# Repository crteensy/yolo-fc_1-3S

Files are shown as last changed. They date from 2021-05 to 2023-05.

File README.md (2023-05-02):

# Yolo FC, STM32F7, 1-3S
This FC has been test flown with a 3" toothpick, and it flew well.

- Main MCU: STM32F745
- IMU: ICM-20602
- Flash: 8MB
- Baro: BMP280
- OSD: '7456
- GNSS: Integrated GPS module (uBlox ZOE-M8Q) with u.Fl connector and experimental support for active antennas
- 4 ESCs:
  - EFM8BB21 / bluejay
  - Calculated current rating of 20A continuous 30A burst (depending on the airflow cooling situation)
- Current sensor: INA186 with 0m5 shunt - subjectively some of the best current measurements we have seen on any FC
- 4 multi purpose expansion connectors:
  - each with its own UART
  - shared I2C bus
  - 5V, 3V3 and GND
  - a multi-purpose pin for analog RSSI, Buzzer, LEDs, etc.
- One video expansion connector:
  - Camera in and VTx out
  - UART
  - 2 multi-purpose pins
  - switchable 5V (*)
- size: 30 x 25.2 mm

The expansion connectors can be used with very simple or more complex plug-ins for
- Rx of your choice
- Magnetometer
- Buzzer
- LED strip
- dual camera switching on the OSD connector
- even additional plugin ESCs for hexa- and octocopters are possible

*) The OSD connector has a 5V output that is only ON when USB is not plugged in. This protects your USB port from power hungry VTx'es that might overload the port. However, that feature can be disabled with a solder bridge.

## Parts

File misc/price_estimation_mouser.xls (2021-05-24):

C6 | 10µF | AMK107ABJ106KAHT | 0.053 | 0.149 | 0.041 | 1
C7 | 100nF | GMK105BJ104KV-F | 0.019 | 0.077 | 0.014 | 1
C8 | 10µF | AMK107ABJ106KAHT | 0.053 | 0.149 | 0.041 | 1
C9 | 100nF | GMK105BJ104KV-F | 0.019 | 0.077 | 0.014 | 1
C10 | 100nF | GMK105BJ104KV-F | 0.019 | 0.077 | 0.014 | 1
C11 | 10µF | AMK107ABJ106KAHT | 0.053 | 0.149 | 0.041 | 1
C12 | 220µF | 6TPE220MAZB | 0.817 | 1.08 | 0.544 | 1
C13 | 220µF | 6TPE220MAZB | 0.817 | 1.08 | 0.544 | 1
C14 | 1µF | LLA215C70G105MA14K | 0.149 | 0.248 | 0.066 | 1
C15 | 2.2µF | LLA219C70G225MA01L | 0.127 | 0.213 | 0.066 | 1
C16 | 100nF | GMK105BJ104KV-F | 0.019 | 0.077 | 0.014 | 1
C17 | 100nF | GMK105BJ104KV-F | 0.019 | 0.077 | 0.014 | 1
C18 | 100nF | GMK105BJ104KV-F | 0.019 | 0.077 | 0.014 | 1
C19 | 100nF | GMK105BJ104KV-F | 0.019 | 0.077 | 0.014 | 1
C20 | 1µF | LLA215C70G105MA14K | 0.149 | 0.248 | 0.066 | 1
C21 | 2.2µF | LLA219C70G225MA01L | 0.127 | 0.213 | 0.066 | 1
C22 | 2.2µF | GRM188R6YA475KE15D | 0.11 | 0.113 | 0.104 | 1
C23 | 2.2µF | GRM188R6YA475KE15D | 0.11 | 0.113 | 0.104 | 1
C24 | 2.2µF | GRM188R6YA475KE15D | 0.11 | 0.113 | 0.104 | 1
C25 | 2.2µF | GRM188R6YA475KE15D | 0.11 | 0.113 | 0.104 | 1
C26 | 10µF | TCJA106M025R0150 | 0.351 | 0.512 | 0.212 | 1
C27 | 10µF | TCJA106M025R0150 | 0.351 | 0.512 | 0.212 | 1
C28 | 100nF | C0603X5R1E104K030BB | 0.037 | 0.03 | 0.022 | 1
C29 | 100nF | GMK105BJ104KV-F | 0.019 | 0.077 | 0.014 | 1
C30 | 100nF | GMK105BJ104KV-F | 0.019 | 0.077 | 0.014 | 1
C31 | 100nF | GMK105BJ104KV-F | 0.019 | 0.077 | 0.014 | 1
C32 | 100nF | GMK105BJ104KV-F | 0.019 | 0.077 | 0.014 | 1
C33 | 100nF | C0603X5R1E104K030BB | 0.037 | 0.03 | 0.022 | 1
C34 | 100nF | GMK105BJ104KV-F | 0.019 | 0.077 | 0.014 | 1
C35 | 10µF |  | 0.077 | 0.114 | 0.69 | 1
C36 | 10µF |  | 0.077 | 0.114 | 0.69 | 1
C37 | 1µF | EMK105BJ105MVHF | 0.025 | 0.038 | 0.022 | 1
C38 | 100nF | C0603X5R1E104K030BB | 0.037 | 0.03 | 0.022 | 1
C39 | 10µF | AMK107ABJ106KAHT | 0.053 | 0.149 | 0.041 | 1
C40 | 100µF | T55A107M6R3C0045 | 0.418 | 0.739 | 0.369 | 1
C41 | 1µF | LLA215C70G105MA14K | 0.149 | 0.248 | 0.066 | 1
C42 | 2.2µF | LLA219C70G225MA01L | 0.127 | 0.213 | 0.066 | 1
C43 | 1µF | LLA215C70G105MA14K | 0.149 | 0.248 | 0.066 | 1
C44 | 2.2µF | LLA219C70G225MA01L | 0.127 | 0.213 | 0.066 | 1
C45 | 2.2µF | GRM188R6YA475KE15D | 0.11 | 0.113 | 0.104 | 1
C46 | 2.2µF | GRM188R6YA475KE15D | 0.11 | 0.113 | 0.104 | 1
C47 | 100nF | C0603X5R1E104K030BB | 0.037 | 0.03 | 0.022 | 1
C48 | 47µF | TCSOM0J476M8R-ZM1 | 0.718 | 0.432 | 0.381 | 1
C49 | 22µF | TCSOM0J476M8R-ZM1 | 0.781 | 0.432 | 0.381 | 1
C50 | 2.2µF | C0402C225M9PACTU | 0.093 | 0.08 | 0.043 | 1
C51 | 2.2µF | C0402C225M9PACTU | 0.093 | 0.08 | 0.043 | 1
C52 | 2.2µF | C0402C225M9PACTU | 0.093 | 0.08 | 0.043 | 1
C54 | 100nF | C0603X5R1E104K030BB | 0.037 | 0.03 | 0.022 | 1
C55 | 2.2µF | GRM188R6YA475KE15D | 0.11 | 0.113 | 0.104 | 1
C56 | 2.2µF | GRM188R6YA475KE15D | 0.11 | 0.113 | 0.104 | 1
D1 | True Green | SML-LX0201UPGC-TR | 0.224 | 0.091 | 0.075 | 1
D2 | SBR1A30T5-7 | SBR1A30T5-7 | 0.197 | 0.317 | 0.125 | 1
D3 | Blue | SML-LX0201USBC-TR | 0.218 | 0.088 | 0.073 | 1
D4 | White | SML-LX0201NWD-TR | 0.273 | 0.121 | 0.096 | 1
FB3 | 120R@100Mhz | BLM18SG121TN1D | 0.064 | 0.043 | 0.039 | 1
FB4 | 120R@100Mhz | BLM18SG121TN1D | 0.064 | 0.043 | 0.039 | 1
FB5 | 120R@100Mhz | BLM18SG121TN1D | 0.064 | 0.043 | 0.039 | 1
FB6 | 120R@100Mhz | BLM18SG121TN1D | 0.064 | 0.043 | 0.039 | 1
J1 | USB_B_Micro |  | 0.667 | 0.618 | 0.488 | 1
J2 | 10132797-011100LF |  | 0.36 | 0.315 | 0.247 | 1
J3 | 10132797-011100LF |  | 0.36 | 0.315 | 0.247 | 1
J4 | 10132797-011100LF |  | 0.36 | 0.315 | 0.247 | 1
J5 | 10132797-011100LF |  | 0.36 | 0.315 | 0.247 | 1
J6 | 10132797-011100LF |  | 0.36 | 0.315 | 0.247 | 1
L2 | 470nH | MCKK1608TR47MN | 0.281 | 0.211 | 0.145 | 1
L3 | 1µH | SRP2512A-1R0M | 0.333 | 0.237 | 0.171 | 1
L4 | 39nH | MLG0603P39NHT000 | 0.032 | 0.029 | 0.021 | 1
Q1 | DMP2066LSN-7 |  |  |  |  | 1
R1 | 100k |  | 0.05 | 0.02 | 0.01 | 1
R2 | 24k9 |  | 0.05 | 0.02 | 0.01 | 1
R3 | 75R |  | 0.05 | 0.02 | 0.01 | 1
R4 | 10k |  | 0.05 | 0.02 | 0.01 | 1
R5 | 470R |  | 0.05 | 0.02 | 0.01 | 1
R6 | 75R |  | 0.05 | 0.02 | 0.01 | 1
R7 | 470R |  | 0.05 | 0.02 | 0.01 | 1
R8 | 1k |  | 0.05 | 0.02 | 0.01 | 1
R9 | 100R |  | 0.05 | 0.02 | 0.01 | 1
R10 | 470R |  | 0.05 | 0.02 | 0.01 | 1
R11 | 10R |  | 0.05 | 0.02 | 0.01 | 1
R12 | 2k2 |  | 0.05 | 0.02 | 0.01 | 1
R13 | 2k2 |  | 0.05 | 0.02 | 0.01 | 1
R14 | 2k2 |  | 0.05 | 0.02 | 0.01 | 1
R15 | 2k2 |  | 0.05 | 0.02 | 0.01 | 1
R16 | 2k2 |  | 0.05 | 0.02 | 0.01 | 1
R17 | 2k2 |  | 0.05 | 0.02 | 0.01 | 1
R18 | 2k2 |  | 0.05 | 0.02 | 0.01 | 1
R19 | 2k2 |  | 0.05 | 0.02 | 0.01 | 1
R20 | 2k2 |  | 0.05 | 0.02 | 0.01 | 1
R21 | 453k |  | 0.05 | 0.02 | 0.01 | 1
R22 | 100k |  | 0.05 | 0.02 | 0.01 | 1
R23 | 2k2 |  | 0.05 | 0.02 | 0.01 | 1
R24 | 2k2 |  | 0.05 | 0.02 | 0.01 | 1
R25 | 2k2 |  | 0.05 | 0.02 | 0.01 | 1
R26 | 2k2 |  | 0.05 | 0.02 | 0.01 | 1
R27 | 2k2 |  | 0.05 | 0.02 | 0.01 | 1
R28 | 2k2 |  | 0.05 | 0.02 | 0.01 | 1
R29 | 2k2 |  | 0.05 | 0.02 | 0.01 | 1
R30 | 2k2 |  | 0.05 | 0.02 | 0.01 | 1
R31 | 1k |  | 0.05 | 0.02 | 0.01 | 1
R32 | 1k |  | 0.05 | 0.02 | 0.01 | 1
R33 | 1k |  | 0.05 | 0.02 | 0.01 | 1
R34 | 1k |  | 0.05 | 0.02 | 0.01 | 1
R36 | 2k2 |  | 0.05 | 0.02 | 0.01 | 1
R37 | 2k2 |  | 0.05 | 0.02 | 0.01 | 1
R47 | 10k |  | 0.05 | 0.02 | 0.01 | 1
R48 | 1k |  | 0.05 | 0.02 | 0.01 | 1
R49 | 500µR | CST0612-FC-R0005-E | 0.466 | 0.336 | 0.279 | 1
R58 | 1k |  | 0.05 | 0.02 | 0.01 | 1
RN1 | 15k | TC124-FR-0715KL | 0.167 | 0.056 | 0.028 | 1
RN2 | 15k | TC124-FR-0715KL | 0.167 | 0.056 | 0.028 | 1
RN5 | 2k2 | YC104-FR-072K2L | 0.161 | 0.053 | 0.027 | 1
RN6 | 2k2 | YC104-FR-072K2L | 0.161 | 0.053 | 0.027 | 1
RN7 | 15k | TC124-FR-0715KL | 0.167 | 0.056 | 0.028 | 1
RN9 | 2k2 | YC104-FR-072K2L | 0.161 | 0.053 | 0.027 | 1
RN13 | 2k2 | YC104-FR-072K2L | 0.161 | 0.053 | 0.027 | 1
RN14 | 2k2 | YC104-FR-072K2L | 0.161 | 0.053 | 0.027 | 1
RN15 | 2k2 | YC104-FR-072K2L | 0.161 | 0.053 | 0.027 | 1
RN16 | 15k | TC124-FR-0715KL | 0.167 | 0.056 | 0.028 | 1
RN18 | 2k2 | YC104-FR-072K2L | 0.161 | 0.053 | 0.027 | 1
RN20 | 2k2 | YC104-FR-072K2L | 0.161 | 0.053 | 0.027 | 1
TP1 | PAD_B_ESC1 |  |  |  |  | 1
TP2 | PAD_A_ESC1 |  |  |  |  | 1
TP3 | PAD_B_ESC1 |  |  |  |  | 1
TP4 | PAD_C_ESC1 |  |  |  |  | 1
TP5 | PAD_B_ESC1 |  |  |  |  | 1
TP6 | PAD_C_ESC1 |  |  |  |  | 1
TP7 | PAD_C_ESC1 |  |  |  |  | 1
TP8 | PAD_A_ESC1 |  |  |  |  | 1
TP9 | BattPad+ |  |  |  |  | 1
TP10 | BattPad- |  |  |  |  | 1
TP11 | PAD_A_ESC1 |  |  |  |  | 1
TP12 | PAD_B_ESC1 |  |  |  |  | 1
TP13 | PAD_C_ESC1 |  |  |  |  | 1
TP14 | PAD_A_ESC1 |  |  |  |  | 1
TP15 | Prog |  |  |  |  | 1
TP16 | Prog |  |  |  |  | 1
TP17 | Prog |  |  |  |  | 1
TP18 | Prog |  |  |  |  | 1
TP19 | Prog |  |  |  |  | 1
TP20 | Prog |  |  |  |  | 1
TP21 | Prog |  |  |  |  | 1
TP22 | Prog |  |  |  |  | 1
TP23 | bridge |  |  |  |  | 1
TP29 | bridge |  |  |  |  | 1
TP30 | pad |  |  |  |  | 1
U1 | EFM8BB21F16G-C-QFN20R | EFM8BB21F16G-C-QFN20R | 0.59 | 0.556 | 0.556 | 1
U2 | EFM8BB21F16G-C-QFN20R | EFM8BB21F16G-C-QFN20R | 0.59 | 0.556 | 0.556 | 1
U3 | NCP81253MNTBG | NCP81253MNTBG | 0.64 | 0.413 | 0.272 | 1
U4 | SiZ200DT | SIZ200DT-T1-GE3 | 0.526 | 0.365 | 0.328 | 1
U6 | EFM8BB21F16G-C-QFN20R | EFM8BB21F16G-C-QFN20R | 0.59 | 0.556 | 0.556 | 1
U7 | NCP81253MNTBG | NCP81253MNTBG | 0.64 | 0.413 | 0.272 | 1
U8 | SiZ200DT | SIZ200DT-T1-GE3 | 0.526 | 0.365 | 0.328 | 1
U9 | NCP81253MNTBG | NCP81253MNTBG | 0.64 | 0.413 | 0.272 | 1
U10 | NCP81253MNTBG | NCP81253MNTBG | 0.64 | 0.413 | 0.272 | 1
U11 | SiZ200DT | SIZ200DT-T1-GE3 | 0.526 | 0.365 | 0.328 | 1
U12 | NCP81253MNTBG | NCP81253MNTBG | 0.64 | 0.413 | 0.272 | 1
U13 | SiZ200DT | SIZ200DT-T1-GE3 | 0.526 | 0.365 | 0.328 | 1
U14 | TPS62821 |  | 1.01 | 0.734 | 0.478 | 1
U15 | SiZ200DT | SIZ200DT-T1-GE3 | 0.526 | 0.365 | 0.328 | 1
U16 | NCP81253MNTBG | NCP81253MNTBG | 0.64 | 0.413 | 0.272 | 1
U17 | NCP81253MNTBG | NCP81253MNTBG | 0.64 | 0.413 | 0.272 | 1
U18 | NCP81253MNTBG | NCP81253MNTBG | 0.64 | 0.413 | 0.272 | 1
U19 | NCP81253MNTBG | NCP81253MNTBG | 0.64 | 0.413 | 0.272 | 1
U20 | SiZ200DT | SIZ200DT-T1-GE3 | 0.526 | 0.365 | 0.328 | 1
U21 | SiZ200DT | SIZ200DT-T1-GE3 | 0.526 | 0.365 | 0.328 | 1
U22 | SiZ200DT | SIZ200DT-T1-GE3 | 0.526 | 0.365 | 0.328 | 1
U23 | SiZ200DT | SIZ200DT-T1-GE3 | 0.526 | 0.365 | 0.328 | 1
U24 | EFM8BB21F16G-C-QFN20R | EFM8BB21F16G-C-QFN20R | 0.59 | 0.556 | 0.556 | 1
U25 | NCP81253MNTBG | NCP81253MNTBG | 0.64 | 0.413 | 0.272 | 1
U26 | SiZ200DT | SIZ200DT-T1-GE3 | 0.526 | 0.365 | 0.328 | 1
U27 | NCP81253MNTBG | NCP81253MNTBG | 0.64 | 0.413 | 0.272 | 1
U28 | NCP81253MNTBG | NCP81253MNTBG | 0.64 | 0.413 | 0.272 | 1
U29 | SiZ200DT | SIZ200DT-T1-GE3 | 0.526 | 0.365 | 0.328 | 1
U30 | SiZ200DT | SIZ200DT-T1-GE3 | 0.526 | 0.365 | 0.328 | 1
U31 | INA186 | INA186A2IDCKR | 1.12 | 0.811 | 0.529 | 1
U32 | LMR33630CQRNX |  | 8.88 | 7.5 | 7.13 | 1
U33 | STM32F745VGHx |  | 8.88 | 7.5 | 7.13 | 1
U34 | AB7456 |  | 2.387 | 2.255 | 2.18 | 1
U35 | ZOE-M8Q_ZOE-M8Q |  | 29 | 14.7 | 14.7 | 1
U36 | ICM-20602 |  | 2.26 | 1.59 | 1.25 | 1
U37 | S25FL064L |  | 2.25 | 1.97 | 1.75 | 1
U39 | BMP280 |  | 2.3 | 1.61 | 1.26 | 1
X1 | Molex_734120110 |  | 0.445 | 0.39 | 0.306 | 1
Y1 | CSTNE8M00G550000R0 |  | 0.184 | 0.147 | 0.131 | 1
Y2 | ECS-270-8-47Q-CES-TR | ECS-270-8-47Q-CES-TR | 0.548 | 0.452 | 0.375 | 1
 |  |  | Price @ 10 | Price @ 100 | Price @ 1k
 |  |  | 91.59 € | 66.15 € | 56.20 €

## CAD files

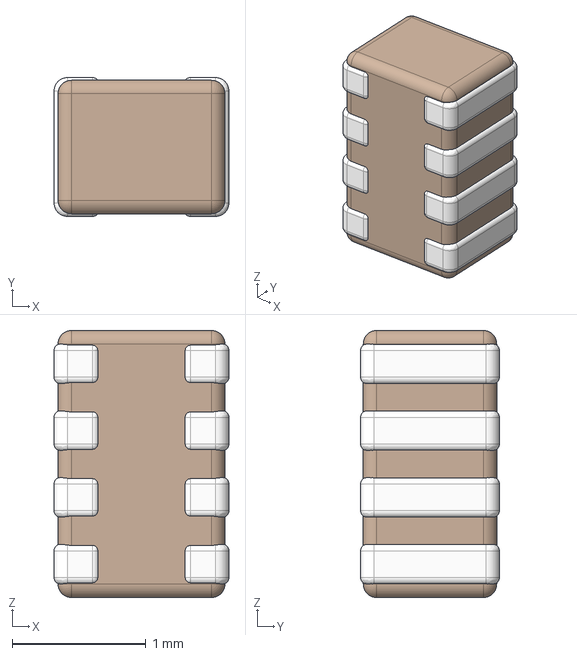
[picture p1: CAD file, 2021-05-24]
3D/idc.stp
1.31 x 1.04 x 2.00 mm

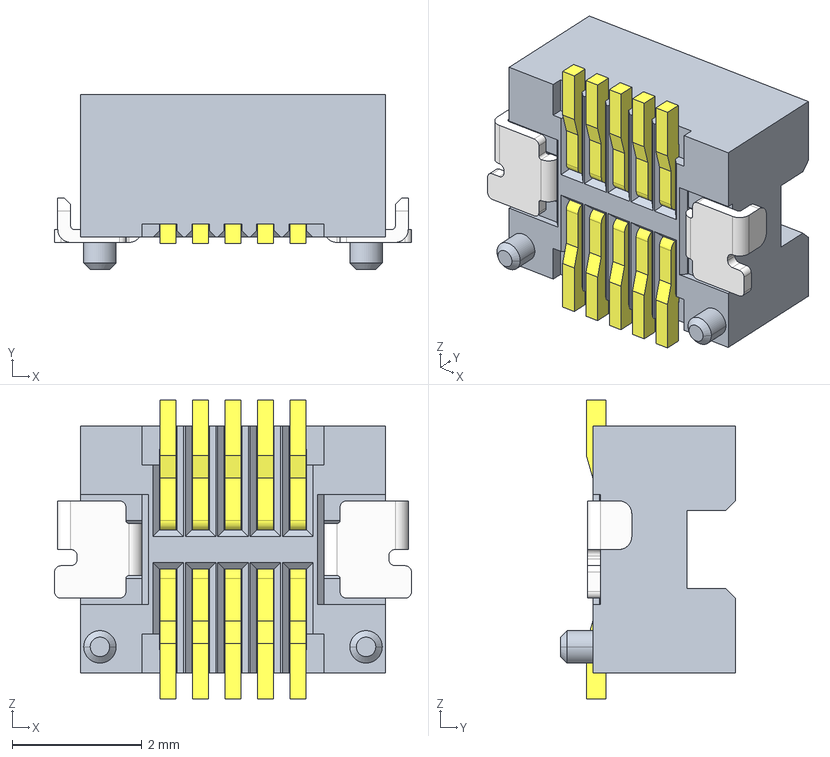
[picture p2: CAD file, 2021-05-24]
3D/10132797-011100LF.stp
5.50 x 2.70 x 4.60 mm
30H-10PIN-F-H
30H-F-TERMINAL x 5

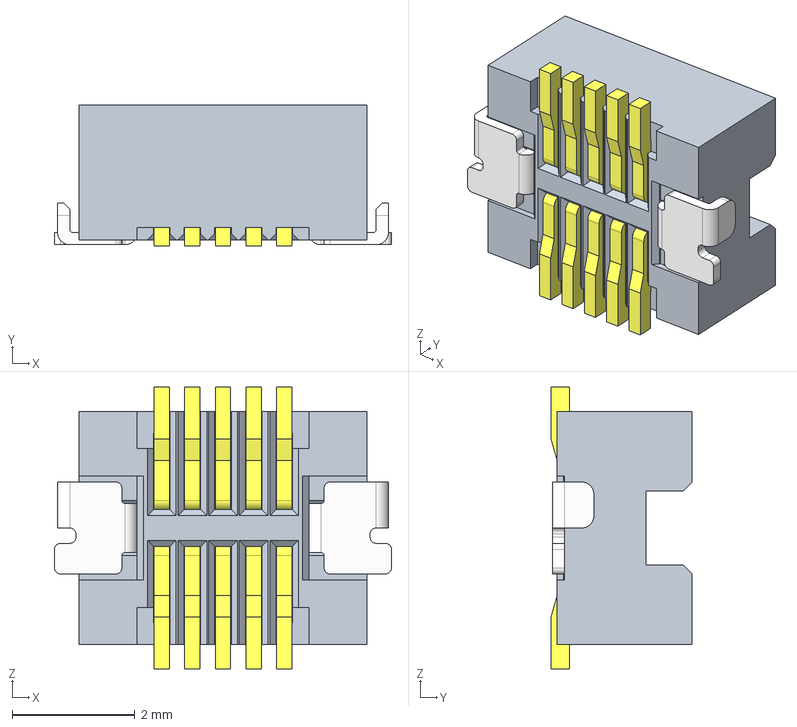
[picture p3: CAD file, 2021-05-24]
3D/10132797-011110LF.stp
5.50 x 2.30 x 4.60 mm
30H-10PIN-F-H
30H-F-TERMINAL x 5

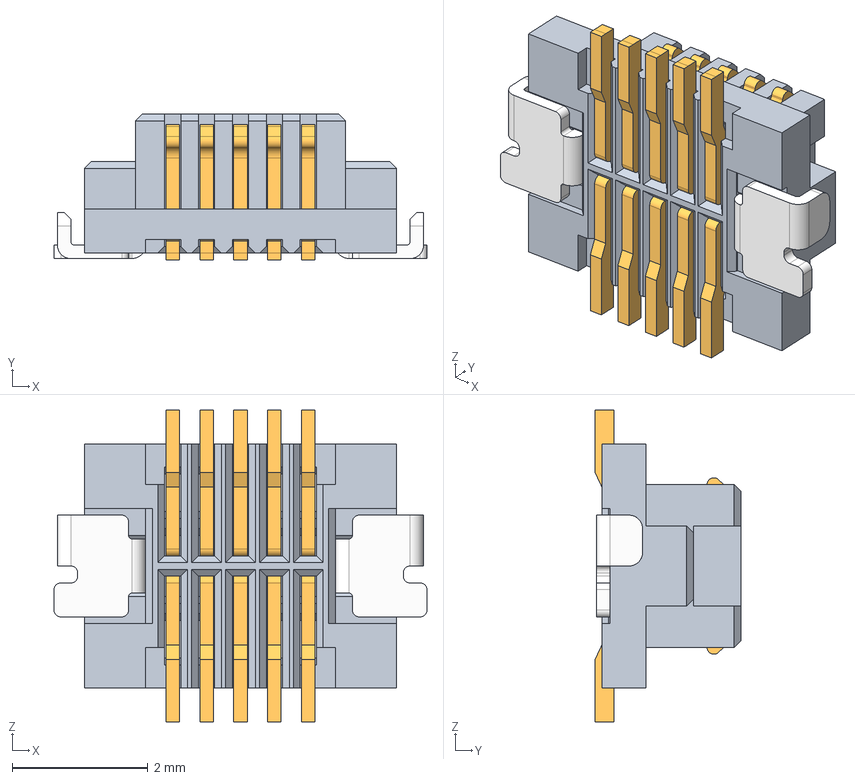
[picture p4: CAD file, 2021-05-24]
3D/10132798-011110LF.stp
5.50 x 2.15 x 4.60 mm
30H-10PIN-M-H
30H-M-TERMINAL x 5

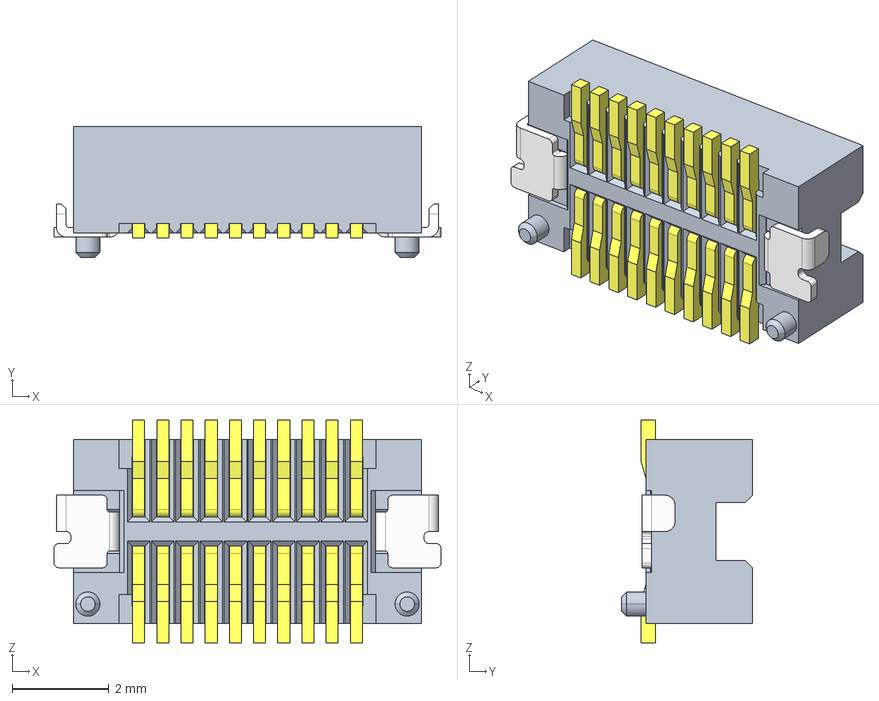
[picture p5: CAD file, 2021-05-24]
3D/10132797-021100LF.stp
8.00 x 2.70 x 4.60 mm
30H-20PIN-F-H
30H-F-TERMINAL x 10

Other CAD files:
10132797-011100LF.stp
10132797-021100LF.stp

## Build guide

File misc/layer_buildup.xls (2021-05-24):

Layer | Type | Thickness
Top | Cu 35µm | 35
 | 2x Prepreg 1080 or similar | 140
In1 | Cu 18µm | 18
 | Core 50 μm | 50
In2 | Cu 18µm | 18
 | 2x Prepreg 1080 or similar | 140
In3 | Cu 35µm | 35
 | Core 50 μm | 50
In4 | Cu 35µm | 35
 | 2x Prepreg 1080 or similar | 140
In5 | Cu 18µm | 18
 | Core 50 μm | 50
IN6 | Cu 18µm | 18
 | 2x Prepreg 1080 or similar | 140
Bot | Cu 35µm | 35
 |  | 922

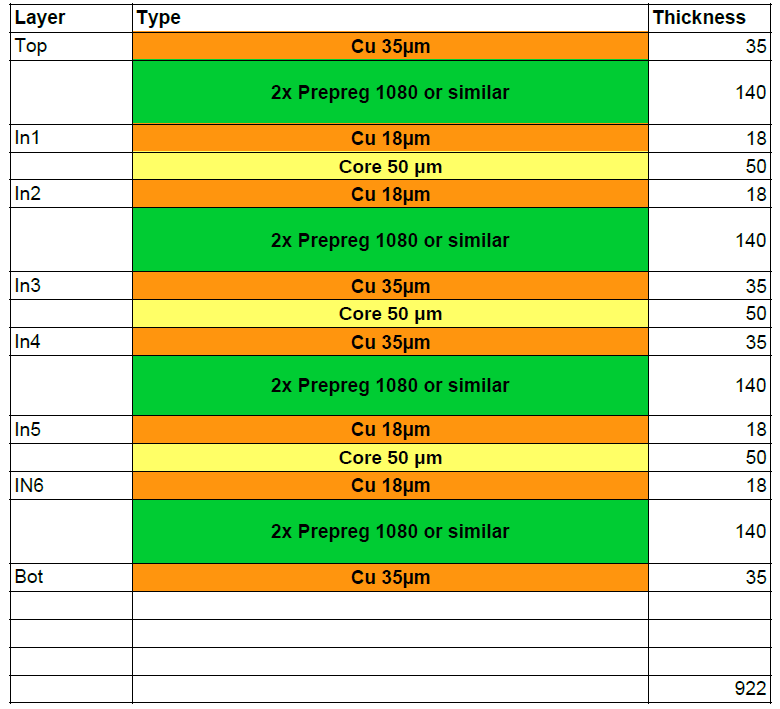
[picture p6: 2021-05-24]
misc/layer_buildup.png

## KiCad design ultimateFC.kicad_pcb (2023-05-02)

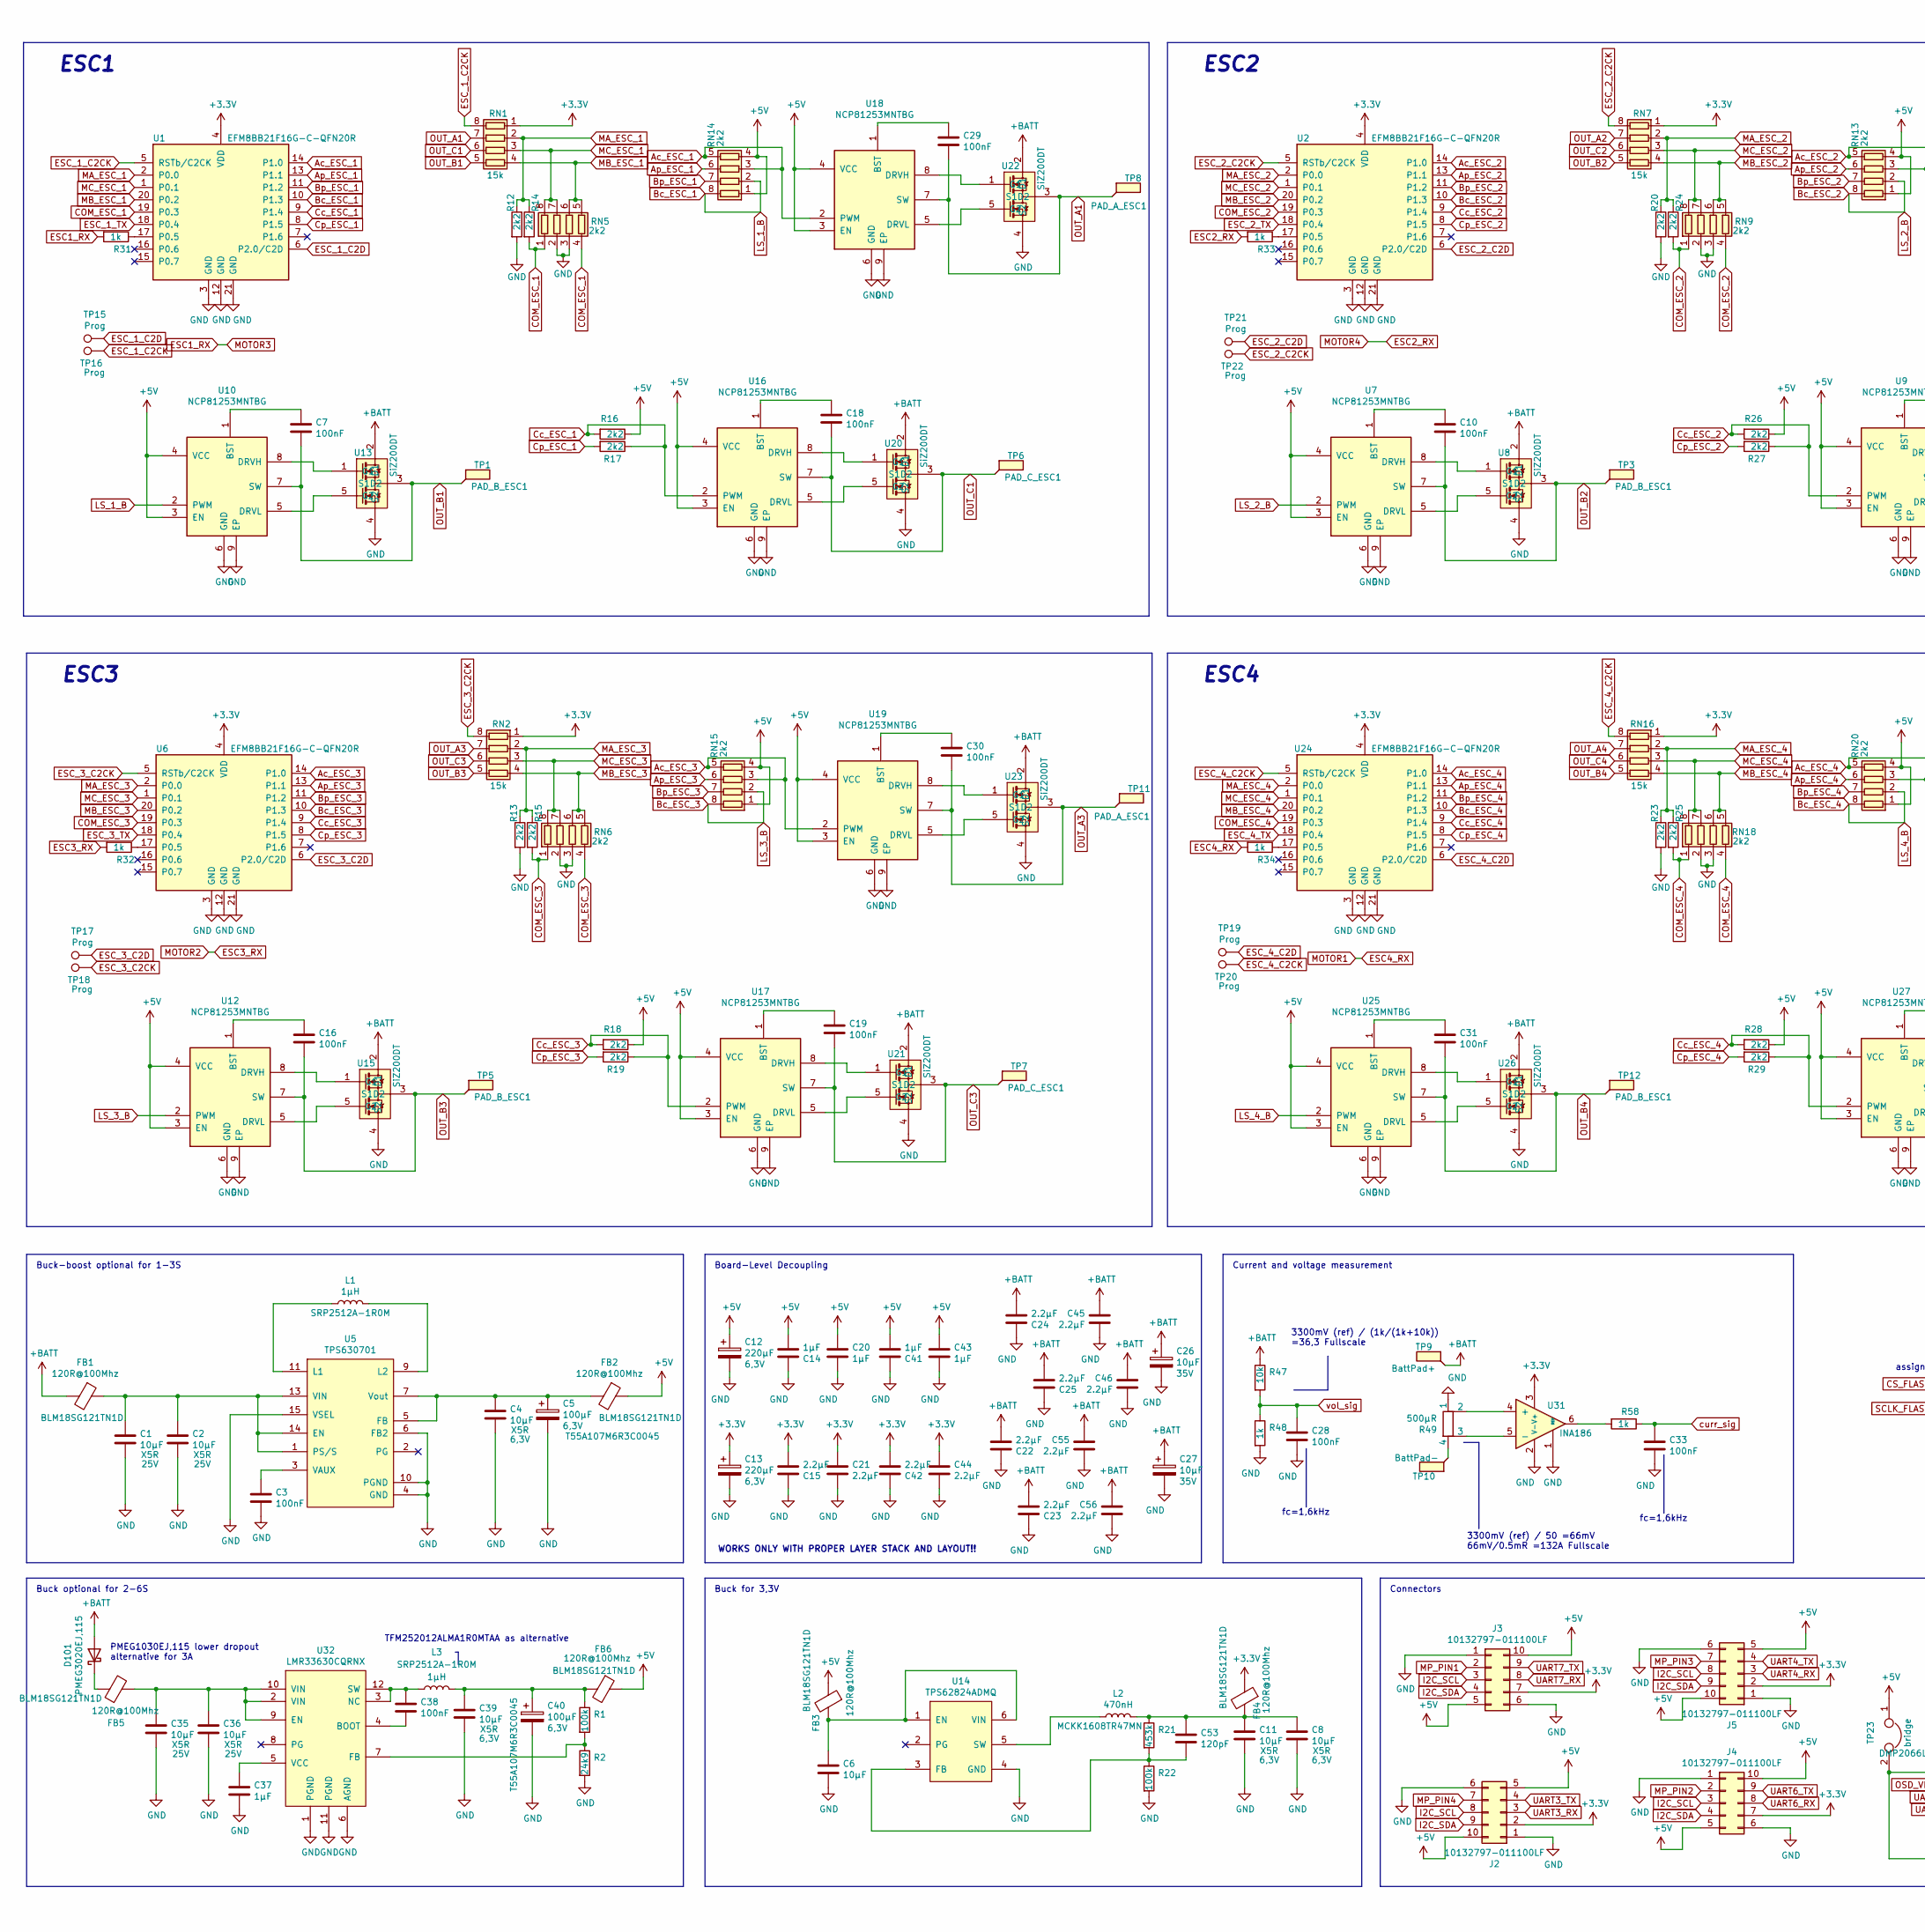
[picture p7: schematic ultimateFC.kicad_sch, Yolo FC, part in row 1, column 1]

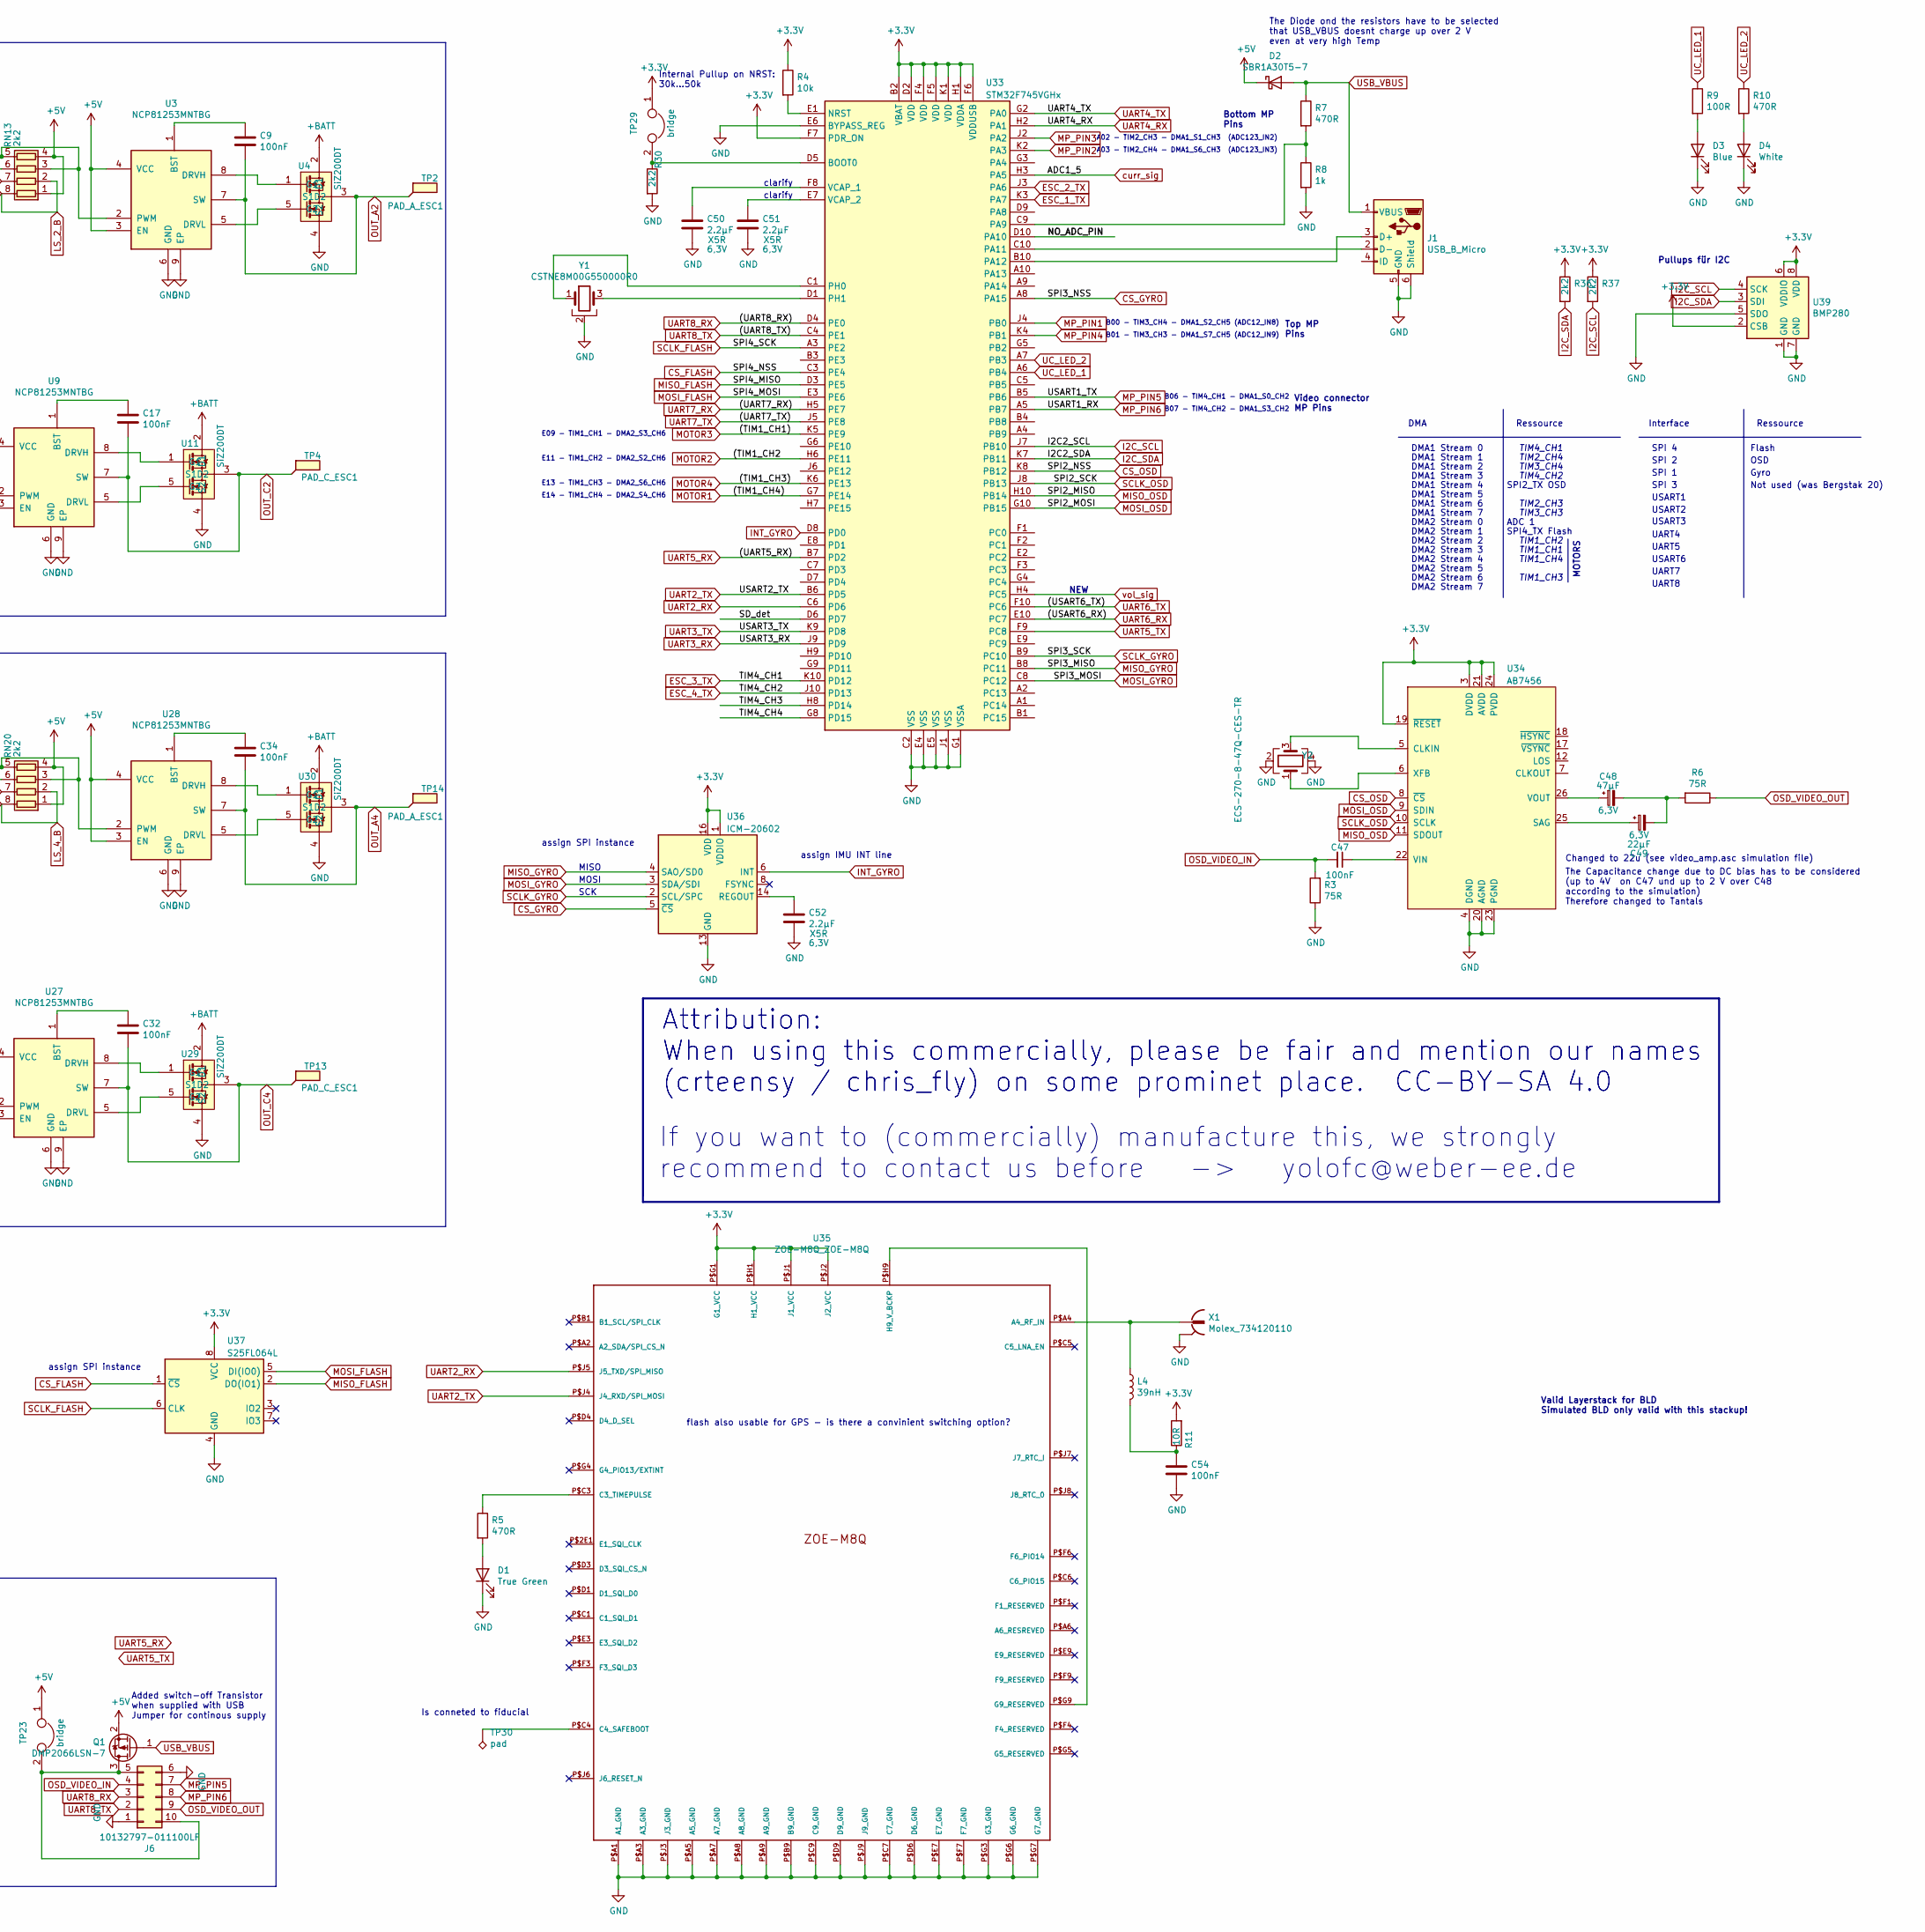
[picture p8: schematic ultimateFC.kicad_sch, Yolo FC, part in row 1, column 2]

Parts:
C1, C2, C35, C36: 10µF; C_1206_3216Metric
C3, C28, C33, C38, C47, C54: 100nF; C_0201_0603Metric_mod
C4, C6, C8, C11, C39: 10µF; C_0603_1608Metric
C5, C40: 100µF; CP_EIA-3216-10_Kemet-I
C7, C9, C10, C16, C17, C18, C19, C29, C30, C31, C32, C34: 100nF; C_0402_1005Metric
C12, C13: 220µF; CP_EIA-3528-15_AVX-H
C14, C20, C41, C43: 1µF; C_AVX_Super_Low_ESL
C15, C21, C42, C44: 2.2µF; C_AVX_Super_Low_ESL
C22, C23, C24, C25, C45, C46, C55, C56: 2.2µF; C_0603_1608Metric
C26, C27: 10µF; CP_EIA-3216-18_Kemet-A
C37: 1µF; C_0402_1005Metric
C48: 47µF; C_0603_1608Metric
C49: 22µF; C_0603_1608Metric
C50, C51, C52: 2.2µF; C_0402_1005Metric
C53: 120pF; C_0201_0603Metric_mod
D1: True Green; LED_0201_0603Metric
D2: SBR1A30T5-7; D_SOD-523
D3: Blue; LED_0201_0603Metric
D4: White; LED_0201_0603Metric
D101: PMEG3020EJ,115; D_SOD-323
FB1, FB2, FB3, FB4, FB5, FB6: 120R@100Mhz; L_0603_1608Metric
J1: USB_B_Micro; USB_Micro-B_Molex_47346-0001
J2, J3, J4, J5, J6: 10132797-011100LF
L1, L3: 1µH; L_Wuerth_MAPI-2506
L2: 470nH; L_0603_1608Metric
L4: 39nH; L_0201_0603Metric
Q1: DMP2066LSN-7; SOT-323_SC-70
R1, R22: 100k; R_0201_0603Metric_mod
R2: 24k9; R_0201_0603Metric_mod
R3, R6: 75R; R_0402_1005Metric
R4: 10k; R_0201_0603Metric_mod
R5, R7, R10: 470R; R_0201_0603Metric_mod
R8, R31, R32, R33, R34, R48, R58: 1k; R_0201_0603Metric_mod
R9: 100R; R_0201_0603Metric_mod
R11: 10R; R_0201_0603Metric_mod
R12, R13, R14, R15, R16, R17, R18, R19, R20, R23, R24, R25, R26, R27, R28, R29, R30, R36, R37: 2k2; R_0201_0603Metric_mod
R21: 453k; R_0201_0603Metric_mod
R47: 10k; R_0402_1005Metric
R49: 500µR; R_Shunt_Vishay_WSKW0612
RN1, RN2, RN7, RN16: 15k; R_Array_Convex_4x0402
RN5, RN6, RN9, RN13, RN14, RN15, RN18, RN20: 2k2; EXB18V_0201x4
TP1, TP3, TP5, TP12: PAD_B_ESC1; esc_pad
TP2, TP8, TP11, TP14: PAD_A_ESC1; esc_pad
TP4, TP6, TP7, TP13: PAD_C_ESC1; esc_pad
TP9: BattPad+; batt_conn_oval
TP10: BattPad-; batt_conn_oval
TP15, TP16, TP17, TP18, TP19, TP20, TP21, TP22: Prog; programm_pad_esc
TP23, TP29: bridge; solderbridge_tiny
TP30: pad; TestPoint_Pad_1.0x1.0mm
U1, U2, U6, U24: EFM8BB21F16G-C-QFN20R; SiliconLabs_QFN-20-1EP_3x3mm_P0.5mm
U3, U7, U9, U10, U12, U16, U17, U18, U19, U25, U27, U28: NCP81253MNTBG; DFN-8-1EP_2x2mm_P0.5mm_EP0.9x1.3mm
U4, U8, U11, U13, U15, U20, U21, U22, U23, U26, U29, U30: SiZ200DT; PowerPAIR3.3x3.3
U5: TPS630701; TEXAS_15-VQFN-HR
U14: TPS62824ADMQ; VSON_HR6
U31: INA186; SOT-363_SC-70-6
U32: LMR33630CQRNX; Texas_RNX0012B
U33: STM32F745VGHx; TFBGA-100_8x8mm_Layout10x10_P0.8mm
U34: AB7456; TSSOP-28_4.4x9.7mm_P0.65mm
U35: ZOE-M8Q_ZOE-M8Q; ZOE-M8
U36: ICM-20602; LGA-16_3x3mm_P0.5mm_LayoutBorder3x5y
U37: S25FL064L; WSON-8_4x4mm_P0.8mm
U39: BMP280; Bosch_LGA-8_2x2.5mm_P0.65mm_ClockwisePinNumbering
X1: Molex_734120110
Y1: CSTNE8M00G550000R0; Resonator_SMD_muRata_CSTxExxV-3Pin_3.0x1.1mm
Y2: ECS-270-8-47Q-CES-TR; ECX-1247Q

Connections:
+3V3: C13.1, C15.2, C21.1, C42.2, C44.1, FB4.1, J2.2, J3.7, J4.7, J5.2, R4.1, R11.2, R36.1, R37.1, RN1.1 (R1.1), RN2.1 (R1.1), RN7.1 (R1.1), RN16.1 (R1.1), TP29.1, U1.4 (VDD), U2.4 (VDD), U6.4 (VDD), U24.4 (VDD), U31.3 (V+), U33.B2 (VBAT), U33.D2 (VDD), U33.F4 (VDD), U33.F5 (VDD), U33.F6 (VDDUSB), U33.F7 (PDR_ON), U33.H1 (VDDA), U33.K1 (VDD), U34.3 (DVDD), U34.19 (~RESET), U34.21 (AVDD), U34.24 (PVDD), U35.P$G1 (G1_VCC), U35.P$H1 (H1_VCC), U35.P$J1 (J1_VCC), U35.P$J2 (J2_VCC), U36.1 (VDDIO), U36.16 (VDD), U37.8 (VCC), U39.2 (CSB), U39.6 (VDDIO), U39.8 (VDD)
+5V: C12.1, C14.2, C20.1, C41.2, C43.1, D2.1 (K), FB2.1, FB3.1, FB6.1, J2.5, J2.10, J3.5, J3.10, J4.5, J4.10, J5.5, J5.10, Q1.2 (S), R16.1, R18.1, R26.1, R28.1, RN13.1 (R1.1), RN13.4 (R4.1), RN14.1 (R1.1), RN14.4 (R4.1), RN15.1 (R1.1), RN15.4 (R4.1), RN20.1 (R1.1), RN20.4 (R4.1), TP23.1, U3.3 (EN), U3.4 (VCC), U7.3 (EN), U7.4 (VCC), U9.3 (EN), U9.4 (VCC), U10.3 (EN), U10.4 (VCC), U12.3 (EN), U12.4 (VCC), U16.3 (EN), U16.4 (VCC), U17.3 (EN), U17.4 (VCC), U18.3 (EN), U18.4 (VCC), U19.3 (EN), U19.4 (VCC), U25.3 (EN), U25.4 (VCC), U27.3 (EN), U27.4 (VCC), U28.3 (EN), U28.4 (VCC)
+BATT: C22.2, C23.2, C24.2, C25.2, C26.1, C27.1, C45.1, C46.1, C55.1, C56.1, D101.2 (A), FB1.2, R47.1, TP9.1, U4.2 (D1), U8.2 (D1), U11.2 (D1), U13.2 (D1), U15.2 (D1), U20.2 (D1), U21.2 (D1), U22.2 (D1), U23.2 (D1), U26.2 (D1), U29.2 (D1), U30.2 (D1)
/NO_ADC_PIN: U33.D10 (PA10)
/SD_det: U33.D6 (PD7)
/TIM4_CH3: U33.H8 (PD14)
/TIM4_CH4: U33.G8 (PD15)
Ac_ESC_1: RN14.3 (R3.1), RN14.5 (R4.2), U1.14 (P1.0), U18.2 (PWM)
Ac_ESC_2: RN13.3 (R3.1), RN13.5 (R4.2), U2.14 (P1.0), U3.2 (PWM)
Ac_ESC_3: RN15.3 (R3.1), RN15.5 (R4.2), U6.14 (P1.0), U19.2 (PWM)
Ac_ESC_4: RN20.3 (R3.1), RN20.5 (R4.2), U24.14 (P1.0), U28.2 (PWM)
Ap_ESC_1: RN14.6 (R3.2), U1.13 (P1.1)
Ap_ESC_2: RN13.6 (R3.2), U2.13 (P1.1)
Ap_ESC_3: RN15.6 (R3.2), U6.13 (P1.1)
Ap_ESC_4: RN20.6 (R3.2), U24.13 (P1.1)
Bc_ESC_1: RN14.2 (R2.1), RN14.8 (R1.2), U1.10 (P1.3), U10.2 (PWM)
Bc_ESC_2: RN13.2 (R2.1), RN13.8 (R1.2), U2.10 (P1.3), U7.2 (PWM)
Bc_ESC_3: RN15.2 (R2.1), RN15.8 (R1.2), U6.10 (P1.3), U12.2 (PWM)
Bc_ESC_4: RN20.2 (R2.1), RN20.8 (R1.2), U24.10 (P1.3), U25.2 (PWM)
Bp_ESC_1: RN14.7 (R2.2), U1.11 (P1.2)
Bp_ESC_2: RN13.7 (R2.2), U2.11 (P1.2)
Bp_ESC_3: RN15.7 (R2.2), U6.11 (P1.2)
Bp_ESC_4: RN20.7 (R2.2), U24.11 (P1.2)
COM_ESC_1: R14.2, RN5.1 (R1.1), RN5.4 (R4.1), U1.19 (P0.3)
COM_ESC_2: R24.2, RN9.1 (R1.1), RN9.4 (R4.1), U2.19 (P0.3)
COM_ESC_3: R15.2, RN6.1 (R1.1), RN6.4 (R4.1), U6.19 (P0.3)
COM_ESC_4: R25.2, RN18.1 (R1.1), RN18.4 (R4.1), U24.19 (P0.3)
CS_FLASH: U33.C3 (PE4), U37.1 (~CS)
CS_GYRO: U33.A8 (PA15), U36.5 (~CS)
CS_OSD: U33.K8 (PB12), U34.8 (~CS)
Cc_ESC_1: R16.2, R17.1, U1.9 (P1.4), U16.2 (PWM)
Cc_ESC_2: R26.2, R27.1, U2.9 (P1.4), U9.2 (PWM)
Cc_ESC_3: R18.2, R19.1, U6.9 (P1.4), U17.2 (PWM)
Cc_ESC_4: R28.2, R29.1, U24.9 (P1.4), U27.2 (PWM)
Cp_ESC_1: R17.2, U1.8 (P1.5)
Cp_ESC_2: R27.2, U2.8 (P1.5)
Cp_ESC_3: R19.2, U6.8 (P1.5)
Cp_ESC_4: R29.2, U24.8 (P1.5)
ESC1_RX: R31.2, U33.K5 (PE9)
ESC2_RX: R33.2, U33.K6 (PE13)
ESC3_RX: R32.2, U33.H6 (PE11)
ESC4_RX: R34.2, U33.G7 (PE14)
ESC_1_C2CK: RN1.8 (R1.2), TP16.1, U1.5 (RSTb/C2CK)
ESC_1_C2D: TP15.1, U1.6 (P2.0/C2D)
ESC_1_TX: U1.18 (P0.4), U33.K3 (PA7)
ESC_2_C2CK: RN7.8 (R1.2), TP22.1, U2.5 (RSTb/C2CK)
ESC_2_C2D: TP21.1, U2.6 (P2.0/C2D)
ESC_2_TX: U2.18 (P0.4), U33.J3 (PA6)
ESC_3_C2CK: RN2.8 (R1.2), TP18.1, U6.5 (RSTb/C2CK)
ESC_3_C2D: TP17.1, U6.6 (P2.0/C2D)
ESC_3_TX: U6.18 (P0.4), U33.K10 (PD12)
ESC_4_C2CK: RN16.8 (R1.2), TP20.1, U24.5 (RSTb/C2CK)
ESC_4_C2D: TP19.1, U24.6 (P2.0/C2D)
ESC_4_TX: U24.18 (P0.4), U33.J10 (PD13)
GND: C1.2, C2.2, C3.2, C4.2, C5.2, C6.2, C8.2, C11.2, C12.2, C13.2, C14.1, C15.1, C20.2, C21.2, C22.1, C23.1, C24.1, C25.1, C26.2, C27.2, C28.2, C33.2, C35.2, C36.2, C37.2, C39.2, C40.2, C41.1, C42.1, C43.2, C44.2, C45.2, C46.2, C50.2, C51.2, C52.2, C54.2, C55.2, C56.2, D1.1 (K), D3.1 (K), D4.1 (K), J1.5 (GND), J1.6 (Shield), J2.1, J2.6, J3.1, J3.6, J4.1, J4.6, J5.1, J5.6, J6.1, J6.6, R2.2, R3.1, R8.2, R12.2, R13.2, R20.2, R22.2, R23.2, R30.2, R48.2, R49.1, RN5.2 (R2.1), RN5.3 (R3.1), RN6.2 (R2.1), RN6.3 (R3.1), RN9.2 (R2.1), RN9.3 (R3.1), RN18.2 (R2.1), RN18.3 (R3.1), U1.3 (GND), U1.12 (GND), U1.21 (GND), U2.3 (GND), U2.12 (GND), U2.21 (GND), U3.6 (GND), U3.9 (EP), U4.4 (S2), U5.4 (GND), U5.6 (FB2), U5.10 (PGND), U5.15 (VSEL), U6.3 (GND), U6.12 (GND), U6.21 (GND), U7.6 (GND), U7.9 (EP), U8.4 (S2), U9.6 (GND), U9.9 (EP), U10.6 (GND), U10.9 (EP), U11.4 (S2), U12.6 (GND), U12.9 (EP), U13.4 (S2), U14.4 (GND), U15.4 (S2), U16.6 (GND), U16.9 (EP), U17.6 (GND), U17.9 (EP), U18.6 (GND), U18.9 (EP), U19.6 (GND), U19.9 (EP), U20.4 (S2), U21.4 (S2), U22.4 (S2), U23.4 (S2), U24.3 (GND), U24.12 (GND), U24.21 (GND), U25.6 (GND), U25.9 (EP), U26.4 (S2), U27.6 (GND), U27.9 (EP), U28.6 (GND), U28.9 (EP), U29.4 (S2), U30.4 (S2), U31.1 (REF), U31.2 (V-), U32.1 (PGND), U32.6 (AGND), U32.11 (PGND), U33.C2 (VSS), U33.E4 (VSS), U33.E5 (VSS), U33.E6 (BYPASS_REG), U33.G1 (VSSA), U33.J1 (VSS), U34.4 (DGND), U34.20 (AGND), U34.23 (PGND), U35.P$A1 (A1_GND), U35.P$A3 (A3_GND), U35.P$A5 (A5_GND), U35.P$A7 (A7_GND), U35.P$A8 (A8_GND), U35.P$A9 (A9_GND), U35.P$B9 (B9_GND), U35.P$C7 (C7_GND), U35.P$C9 (C9_GND), U35.P$D6 (D6_GND), U35.P$D9 (D9_GND), U35.P$E7 (E7_GND), U35.P$F7 (F7_GND), U35.P$G3 (G3_GND), U35.P$G6 (G6_GND), U35.P$G7 (G7_GND), U35.P$J3 (J3_GND), U35.P$J9 (J9_GND), U36.9 (GND), U36.10 (GND), U36.11 (GND), U36.12 (GND), U36.13 (GND), U36.15 (GND), U37.4 (GND), U39.1 (GND), U39.5 (SDO), U39.7 (GND), X1.S@1 (2), X1.S@2 (2), X1.S@3 (2), Y1.2, Y2.2, Y2.4
I2C_SCL: J2.8, J3.3, J4.3, J5.8, R37.2, U33.J7 (PB10), U39.4 (SCK)
I2C_SDA: J2.9, J3.4, J4.4, J5.9, R36.2, U33.K7 (PB11), U39.3 (SDI)
INT_GYRO: U33.D8 (PD0), U36.6 (INT)
MA_ESC_1: R12.1, R14.1, RN1.2 (R2.1), U1.2 (P0.0)
MA_ESC_2: R20.1, R24.1, RN7.2 (R2.1), U2.2 (P0.0)
MA_ESC_3: R13.1, R15.1, RN2.2 (R2.1), U6.2 (P0.0)
MA_ESC_4: R23.1, R25.1, RN16.2 (R2.1), U24.2 (P0.0)
MB_ESC_1: RN1.4 (R4.1), RN5.5 (R4.2), RN5.6 (R3.2), U1.20 (P0.2)
MB_ESC_2: RN7.4 (R4.1), RN9.5 (R4.2), RN9.6 (R3.2), U2.20 (P0.2)
MB_ESC_3: RN2.4 (R4.1), RN6.5 (R4.2), RN6.6 (R3.2), U6.20 (P0.2)
MB_ESC_4: RN16.4 (R4.1), RN18.5 (R4.2), RN18.6 (R3.2), U24.20 (P0.2)
MC_ESC_1: RN1.3 (R3.1), RN5.7 (R2.2), RN5.8 (R1.2), U1.1 (P0.1)
MC_ESC_2: RN7.3 (R3.1), RN9.7 (R2.2), RN9.8 (R1.2), U2.1 (P0.1)
MC_ESC_3: RN2.3 (R3.1), RN6.7 (R2.2), RN6.8 (R1.2), U6.1 (P0.1)
MC_ESC_4: RN16.3 (R3.1), RN18.7 (R2.2), RN18.8 (R1.2), U24.1 (P0.1)
MISO_FLASH: U33.D3 (PE5), U37.2 (DO(IO1))
MISO_GYRO: U33.B8 (PC11), U36.4 (SAO/SD0)
MISO_OSD: U33.H10 (PB14), U34.11 (SDOUT)
MOSI_FLASH: U33.E3 (PE6), U37.5 (DI(IO0))
MOSI_GYRO: U33.C8 (PC12), U36.3 (SDA/SDI)
MOSI_OSD: U33.G10 (PB15), U34.9 (SDIN)
MP_PIN1: J3.2, U33.J4 (PB0)
MP_PIN2: J4.2, U33.K2 (PA3)
MP_PIN3: J5.7, U33.J2 (PA2)
MP_PIN4: J2.7, U33.K4 (PB1)
MP_PIN5: J6.7, U33.B5 (PB6)
MP_PIN6: J6.8, U33.A5 (PB7)
unnamed: C1.1, C2.1, FB1.1, U5.1 (PS/S), U5.13 (VIN), U5.14 (EN)
unnamed: C3.1, U5.3 (VAUX)
unnamed: C4.1, C5.1, FB2.2, U5.5 (FB), U5.7 (Vout)
unnamed: C6.1, FB3.2, U14.1 (EN), U14.6 (VIN)
unnamed: C7.1, U10.1 (BST)
unnamed: C9.1, U3.1 (BST)
unnamed: C10.1, U7.1 (BST)
unnamed: C8.1, C11.1, C53.1, FB4.2, L2.2, R21.1
unnamed: C16.1, U12.1 (BST)
unnamed: C17.1, U9.1 (BST)
unnamed: C18.1, U16.1 (BST)
unnamed: C19.1, U17.1 (BST)
unnamed: C29.1, U18.1 (BST)
unnamed: C30.1, U19.1 (BST)
unnamed: C31.1, U25.1 (BST)
unnamed: C32.1, U27.1 (BST)
unnamed: C34.1, U28.1 (BST)
unnamed: C35.1, C36.1, FB5.2, U32.2 (VIN), U32.9 (EN), U32.10 (VIN)
unnamed: C37.1, U32.5 (VCC)
unnamed: C38.1, L3.1, U32.3 (NC), U32.12 (SW)
unnamed: C38.2, U32.4 (BOOT)
unnamed: C39.1, C40.1, FB6.2, L3.2, R1.1
unnamed: C47.1, U34.22 (VIN)
unnamed: C48.1, U34.26 (VOUT)
unnamed: C48.2, C49.2, R6.2
unnamed: C49.1, U34.25 (SAG)
unnamed: C50.1, U33.F8 (VCAP_1)
unnamed: C51.1, U33.E7 (VCAP_2)
unnamed: C52.1, U36.14 (REGOUT)
unnamed: C53.2, R21.2, R22.1, U14.3 (FB)
unnamed: C54.1, L4.2, R11.1
unnamed: D1.2 (A), R5.2
unnamed: D3.2 (A), R9.2
unnamed: D4.2 (A), R10.2
unnamed: D101.1 (K), FB5.1
unnamed: J1.2 (D-), U33.C10 (PA11)
unnamed: J1.3 (D+), U33.B10 (PA12)
unnamed: J6.5, J6.10, Q1.3 (D), TP23.2
unnamed: L1.1, U5.11 (L1)
unnamed: L1.2, U5.9 (L2)
unnamed: L2.1, U14.5 (SW)
unnamed: L4.1, U35.P$A4 (A4_RF_IN), X1.1
unnamed: R1.2, R2.1, U32.7 (FB)
unnamed: R4.2, U33.E1 (NRST)
unnamed: R5.1, U35.P$C3 (C3_TIMEPULSE)
unnamed: R7.2, R8.1, U33.C9 (PA9)
unnamed: R30.1, TP29.2, U33.D5 (BOOT0)
unnamed: R31.1, U1.17 (P0.5)
unnamed: R32.1, U6.17 (P0.5)
unnamed: R33.1, U2.17 (P0.5)
unnamed: R34.1, U24.17 (P0.5)
unnamed: R49.2, U31.4 (+)
unnamed: R49.3, U31.5 (-)
unnamed: R49.4, TP10.1
unnamed: R58.2, U31.6
unnamed: TP30.1, U35.P$C4 (C4_SAFEBOOT)
unnamed: U3.5 (DRVL), U4.5 (G2)
unnamed: U3.8 (DRVH), U4.1 (G1)
unnamed: U7.5 (DRVL), U8.5 (G2)
unnamed: U7.8 (DRVH), U8.1 (G1)
unnamed: U10.5 (DRVL), U13.5 (G2)
unnamed: U10.8 (DRVH), U13.1 (G1)
unnamed: U9.8 (DRVH), U11.1 (G1)
unnamed: U9.5 (DRVL), U11.5 (G2)
unnamed: U12.5 (DRVL), U15.5 (G2)
unnamed: U12.8 (DRVH), U15.1 (G1)
unnamed: U16.5 (DRVL), U20.5 (G2)
unnamed: U16.8 (DRVH), U20.1 (G1)
unnamed: U17.5 (DRVL), U21.5 (G2)
unnamed: U17.8 (DRVH), U21.1 (G1)
unnamed: U18.5 (DRVL), U22.5 (G2)
unnamed: U18.8 (DRVH), U22.1 (G1)
unnamed: U19.5 (DRVL), U23.5 (G2)
unnamed: U19.8 (DRVH), U23.1 (G1)
unnamed: U25.5 (DRVL), U26.5 (G2)
unnamed: U25.8 (DRVH), U26.1 (G1)
unnamed: U27.5 (DRVL), U29.5 (G2)
unnamed: U27.8 (DRVH), U29.1 (G1)
unnamed: U28.5 (DRVL), U30.5 (G2)
unnamed: U28.8 (DRVH), U30.1 (G1)
unnamed: U33.C1 (PH0), Y1.1
unnamed: U33.D1 (PH1), Y1.3
unnamed: U34.5 (CLKIN), Y2.3
unnamed: U34.6 (XFB), Y2.1
unnamed: U35.P$G9 (G9_RESERVED), U35.P$H9 (H9_V_BCKP)
OSD_VIDEO_IN: C47.2, J6.4, R3.2
OSD_VIDEO_OUT: J6.9, R6.1
OUT_A1: C29.2, RN1.7 (R2.2), TP8.1, U18.7 (SW), U22.3 (S1D2)
OUT_A2: C9.2, RN7.7 (R2.2), TP2.1, U3.7 (SW), U4.3 (S1D2)
OUT_A3: C30.2, RN2.7 (R2.2), TP11.1, U19.7 (SW), U23.3 (S1D2)
OUT_A4: C34.2, RN16.7 (R2.2), TP14.1, U28.7 (SW), U30.3 (S1D2)
OUT_B1: C7.2, RN1.5 (R4.2), TP1.1, U10.7 (SW), U13.3 (S1D2)
OUT_B2: C10.2, RN7.5 (R4.2), TP3.1, U7.7 (SW), U8.3 (S1D2)
OUT_B3: C16.2, RN2.5 (R4.2), TP5.1, U12.7 (SW), U15.3 (S1D2)
OUT_B4: C31.2, RN16.5 (R4.2), TP12.1, U25.7 (SW), U26.3 (S1D2)
OUT_C1: C18.2, RN1.6 (R3.2), TP6.1, U16.7 (SW), U20.3 (S1D2)
OUT_C2: C17.2, RN7.6 (R3.2), TP4.1, U9.7 (SW), U11.3 (S1D2)
OUT_C3: C19.2, RN2.6 (R3.2), TP7.1, U17.7 (SW), U21.3 (S1D2)
OUT_C4: C32.2, RN16.6 (R3.2), TP13.1, U27.7 (SW), U29.3 (S1D2)
SCLK_FLASH: U33.A3 (PE2), U37.6 (CLK)
SCLK_GYRO: U33.B9 (PC10), U36.2 (SCL/SPC)
SCLK_OSD: U33.J8 (PB13), U34.10 (SCLK)
UART2_RX: U33.C6 (PD6), U35.P$J5 (J5_TXD/SPI_MISO)
UART2_TX: U33.B6 (PD5), U35.P$J4 (J4_RXD/SPI_MOSI)
UART3_RX: J2.3, U33.J9 (PD9)
UART3_TX: J2.4, U33.K9 (PD8)
UART4_RX: J5.3, U33.H2 (PA1)
UART4_TX: J5.4, U33.G2 (PA0)
UART5_RX: U33.B7 (PD2)
UART5_TX: U33.F9 (PC8)
UART6_RX: J4.8, U33.E10 (PC7)
UART6_TX: J4.9, U33.F10 (PC6)
UART7_RX: J3.8, U33.H5 (PE7)
UART7_TX: J3.9, U33.J5 (PE8)
UART8_RX: J6.3, U33.D4 (PE0)
UART8_TX: J6.2, U33.C4 (PE1)
UC_LED_1: R9.1, U33.A6 (PB4)
UC_LED_2: R10.1, U33.A7 (PB3)
USB_VBUS: D2.2 (A), J1.1 (VBUS), Q1.1 (G), R7.1
curr_sig: C33.1, R58.1, U33.H3 (PA5)
vol_sig: C28.1, R47.2, R48.1, U33.H4 (PC5)

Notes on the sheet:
E11 - TIM1_CH2 - DMA2_S2_CH6
E13 - TIM1_CH3 - DMA2_S6_CH6
Is conneted to fiducial
DMA1 Stream 6
TIM1_CH4
USART3
B07 - TIM4_CH2 - DMA1_S3_CH2
SPI 2
TFM252012ALMA1R0MTAA as alternative
3300mV (ref) / (1k/(1k+10k)) =36,3 Fullscale
Interface
A02 - TIM2_CH3 - DMA1_S1_CH3 (ADC123_IN2)
SPI 1
Attribution: When using this commercially, please be fair and mention our names (crteensy / chris_fly) on some prominet place. CC-BY-SA 4.0
Internal Pullup on NRST: 30k...50k
UART5
SPI2_TX OSD
SPI 4
A03 - TIM2_CH4 - DMA1_S6_CH3 (ADC123_IN3)
TIM4_CH1
DMA1 Stream 5
MOSI
OSD
SPI 3
Valid Layerstack for BLD Simulated BLD only valid with this stackup!
TIM2_CH3
SCK
DMA2 Stream 5
DMA2 Stream 0
UART8
Board-Level Decoupling
DMA1 Stream 7
3300mV (ref) / 50 =66mV 66mV/0.5mR =132A Fullscale
TIM1_CH1
B00 - TIM3_CH4 - DMA1_S2_CH5 (ADC12_IN8)
DMA
Connectors
B01 - TIM3_CH3 - DMA1_S7_CH5 (ADC12_IN9)
Buck-boost optional for 1-3S
USART2

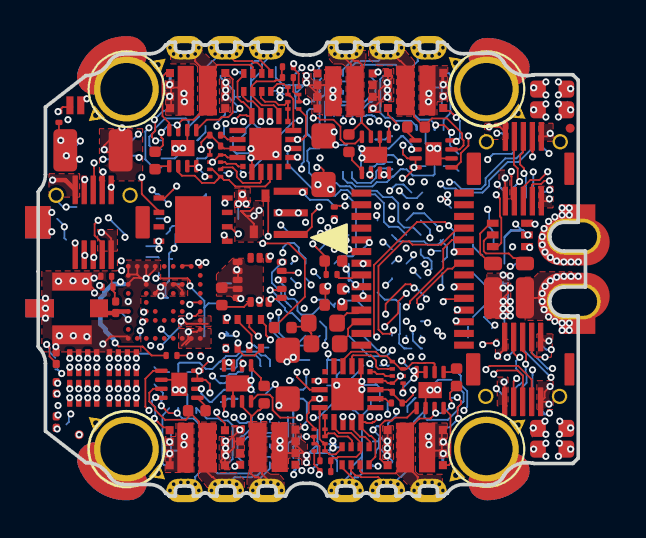
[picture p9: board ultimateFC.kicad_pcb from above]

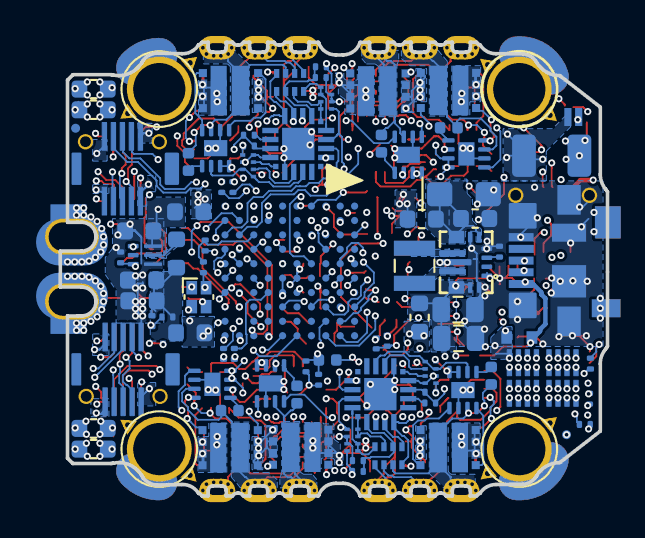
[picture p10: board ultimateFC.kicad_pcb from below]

Board: 8 copper layers, 30.4 x 25.2 mm, 182 parts (90 on the bottom side), 189 nets.

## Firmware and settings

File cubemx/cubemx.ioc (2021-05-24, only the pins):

Mcu.UserName=STM32F745VGHx
PA0/WKUP.Signal=UART4_TX
PA1.Signal=UART4_RX
PA11.Signal=USB_OTG_FS_DM
PA12.Signal=USB_OTG_FS_DP
PA15.Signal=SPI3_NSS
PA2.Signal=S_TIM2_CH3
PA3.Signal=S_TIM2_CH4
PA5.Signal=ADCx_IN5
PA6.Signal=S_TIM3_CH1
PA7.Signal=S_TIM3_CH2
PA9.Signal=USB_OTG_FS_VBUS
PB0.Signal=S_TIM3_CH3
PB1.Signal=S_TIM3_CH4
PB10.Signal=I2C2_SCL
PB11.Signal=I2C2_SDA
PB12.Signal=SPI2_NSS
PB13.Signal=SPI2_SCK
PB14.Signal=SPI2_MISO
PB15.Signal=SPI2_MOSI
PB3.Signal=GPIO_Output
PB4.Signal=GPIO_Output
PB6.Signal=USART1_TX
PB7.Signal=USART1_RX
PC10.Signal=SPI3_SCK
PC11.Signal=SPI3_MISO
PC12.Signal=SPI3_MOSI
PC5.Signal=ADCx_IN15
PC6.Signal=USART6_TX
PC7.Signal=USART6_RX
PD0.Signal=GPIO_Input
PD12.Signal=S_TIM4_CH1
PD13.Signal=S_TIM4_CH2
PD2.Signal=UART5_RX
PD5.Signal=USART2_TX
PD6.Signal=USART2_RX
PD7.Signal=GPIO_Input
PD8.Signal=USART3_TX
PD9.Signal=USART3_RX
PE0.Signal=UART8_RX
PE1.Signal=UART8_TX
PE11.Signal=S_TIM1_CH2
PE13.Signal=S_TIM1_CH3
PE14.Signal=S_TIM1_CH4
PE2.Signal=SPI4_SCK
PE4.Signal=SPI4_NSS
PE5.Signal=SPI4_MISO
PE6.Signal=SPI4_MOSI
PE7.Signal=UART7_RX
PE8.Signal=UART7_TX
PE9.Signal=S_TIM1_CH1
PH0/OSC_IN.Signal=RCC_OSC_IN
PH1/OSC_OUT.Signal=RCC_OSC_OUT

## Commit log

2021-03-30 swap DCDC for 1-3S
    [10132797-011100LF.stp, 10132797-021100LF.stp, ultimateFC_v2.kicad_pcb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]
2021-03-31 update layout
    [ultimateFC_v2.kicad_pcb, ultimateFC_v2.sch]
2021-03-31 update schematic
    [ultimateFC_v2.sch]
2021-03-31 remove references on silk screen
    [ultimateFC_v2.kicad_pcb]
2021-05-24 updated 1-3s to newest board version
    [10132797-011100LF.stp, 10132797-011110LF.stp, 10132797-021100LF.stp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]
2021-05-24 update schematic pdf, add cubemx
2021-08-04 add assembly_output/*.pos
    [ultimateFC-bottom-pos.csv, ultimateFC-top-pos.csv]
2021-08-23 update footprints to reflect surface mounting update lib update assembly_output/*.pos
    [ultimateFC.kicad_pcb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]
2021-08-24 fix fidu centers, update pos files
    [ultimateFC.kicad_pcb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]
2021-09-17 fix DCDC footprint, remove some silkscreen
    [ultimateFC.kicad_pcb]
2022-03-27 update pcb to KiCad6 add assembly output gerbers
    [ultimateFC.kicad_pcb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]
2023-05-02 cleanup before publish
    [ultimateFC-B_Cu.gbr, ultimateFC-B_Mask.gbr, ultimateFC-B_Paste.gbr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]
2023-05-02 fix paste for 0201 components
    [ultimateFC.kicad_pcb, ultimateFC.sch]
